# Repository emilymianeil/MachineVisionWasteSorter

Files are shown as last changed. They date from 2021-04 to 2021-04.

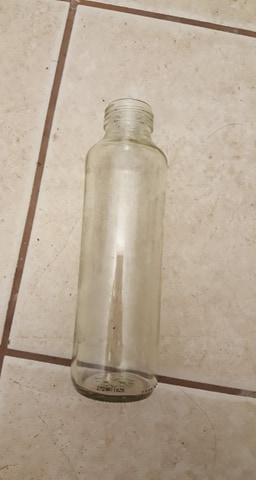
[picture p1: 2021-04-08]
Phase 3-Detail Design/4. Controls/Images/EG/Glass-Clear Bottles/155523304_348365116399683_3477293320346777046_n.jpg

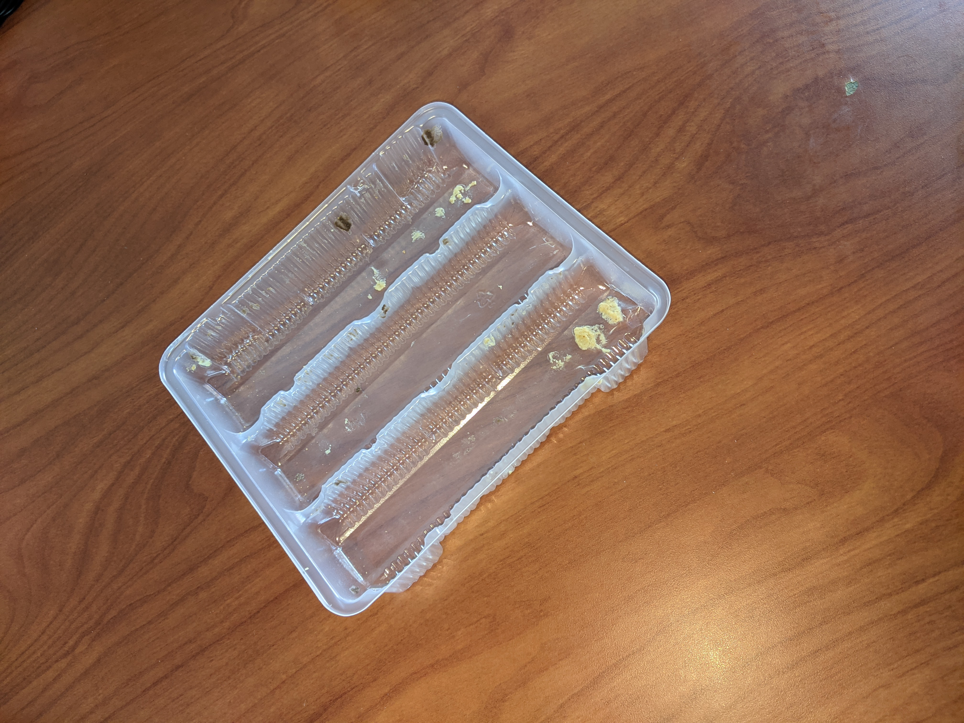
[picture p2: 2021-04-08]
Phase 3-Detail Design/4. Controls/Images/EG/Plastic-Clear/PXL_20210303_194455637.jpg

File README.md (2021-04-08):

# WasteSorter
The group chose to address the Canadian Engineering Grand Challenge’s (EGC) call for inclusive, safe, and sustainable cities by reducing recycling contamination and at improving the accuracy of at home recycling.

The primary function of the project is to take a piece of household waste, identify the type of waste, and sort it into its respective category. The design goals considered safety, environmental impact, public acceptance, reliability, performance, ease of use, maintenance, and standardization. The design criteria specifications were sorting accuracy, composition of product, safety standards, lifespan, cost, sorting, power consumption, system complexity.

To use the product, users must download the controls software onto a Jetson. Users then must 3D print or manufacture parts, order the custom PCB, and assemble the electro-mechanical system. Finally, the user must download the mobile application, and connect to the Jetson via Bluetooth.

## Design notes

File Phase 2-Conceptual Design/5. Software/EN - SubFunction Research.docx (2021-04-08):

# Executive Summary – Solution Evaluation

The following sub-functions were rated against each criteria by the ‘average’ solutions; I just put an estimate of how the common solution will perform, and then we can actually decide what specific solution we want and/or conduct further research to find the best tool for our team.

Specification | Image Processing | | IoT + App/Website | | Voice Commands | | Gesture Control | | Microprocessor
Sorting accuracy | >=75% | 10 | N/A | 10 | N/A | 10 | N/A | 10 | N/A | 10
Composition | N/A | 10 | N/A | 10 | N/A | 10 | Raw material | 0 | Raw material | 0
Safety Standards | ? | ? | ? | ? | ? | ? | Met (Jetson Nano) | 10 | Met | 10
Lifespan | N/A | 10 | N/A | 10 | N/A (depending on input) | 10 | ?? | 10 | ~5 yrs | 5
Cost | $0 | 10 | $35-$110 | 5 | $0-$7 | 9 | $100 | 2 | $25-$100 | 5
Sorting | ~2-5 seconds | 5 | ~2-5 seconds (TCP) | 5 | N/A | 10 | N/A | 10 | ~2-5 seconds (TCP + BT/Wifi) | 5
Power consumption | 7-12V | 7 | N/A (cloud computing) | 10 | N/A | 10 | 5V | 10 | 7-12V | 7
System Complexity | Requires Cam | 8 | Requires BT/wifi + cloud | 7 | Easy implementation | 9 | Good | 9 | Required for most functions | 8

*Note: photos for image detection (Trashnet) were taken by an iPhone 5, iPHone 7 and iPhone SE. If we choose this solution, we need to either use common phone, or use a camera with similar specifications if we are assuming the same efficacy rate. If not, we need to train the model with an entirely new set to get an efficacy rate.

*Note: Microprocessor can be used for LCD+Buttons, Touch Screen, loT+App/Website, general logic

*Note: I’m assuming a cost of $0 for phone usage (assuming user already has phone)

**Need to find lifespan of Jetson nano

# Sub-Function Solutions Research

## A. Identification – Image Processing

Image processing for waste exists online for free. The following are public Github repos with brief descriptions.

### I. Waste Sorter

Capabilities: Sorts images of into cardboard, glass, metal, paper, plastic, trash at a success rate of 92%. Uses fatsia deep learning framework.

Requirements: Given source files, corresponding dataset (available on the Github README), and Anaconda IDE (free python IDE)

Repository: https://github.com/collindching/Waste-Sorter

### II. Trash Recycling Classifier

Capabilities: Sorts images of into cardboard, glass, metal, paper, plastic, trash. Uses pytorch deep learning framework. Efficiency unknown.

Requirements: Given source files, corresponding dataset (available on the Github README, cloud environment for training (AWS or Google colab).

Repository: https://github.com/winkhai/trash-recycling-classifier

### III. Recycle

Capabilities: Sorts images of glass, metal, and plastic at a success rate of 85%. Uses

Requirements: Given source files, corresponding dataset (available on the Github README), and a python IDE

Repository: https://github.com/ZAFERSHAMIM/recycle

### IV. Trashnet

Capabilities: Sorts images of glass, paper, cardboard, plastic metal and trash at a success rate of 75%. Devices used to take dataset photos were common phones (iPhone 7, iPhone 5, iPHone SE).

Requirements: Given source files, corresponding dataset (available on the Github README), and a python IDE

Repository: https://github.com/garythung/trashnet

## B. IoT + App / Website

We can make an app for free using third party tools or manually (XCode, VS Code)

### I. Android App Builder – MIT App Inventor / App Builder / CodeUp Start

Capabilities: Minimal, low code environments with networking, scalable, compatible with most cloud environments

Cost: $25 (to publish to Google Play)

Source:

https://www.producthunt.com/alternatives/google-app-maker

https://appinventiv.com/blog/how-to-submit-app-to-google-play-store/#:~:text=There%20is%20only%20a%20one,you%20publish%20are%20cost%2Dfree

### II. Apple App Builder – MIT App Inventor / App Builder / CodeUp Start

Capabilities: Minimal, low code environments with networking, scalable, compatible with most cloud environments

Cost: $99 (to publish to App Store)

Source: https://codewithchris.com/submit-your-app-to-the-app-store/#:~:text=In%20order%20to%20be%20able,in%20the%20Apple%20Developer%20Program.&text=It%20costs%20%2499%2Fyear%20but,Stores%20on%20all%20Apple%20platforms

### III. Manual App Builder – XCode / VS Code

Capabilities: High code environments with networking, scalable, compatible with most cloud environments (but a lot of boiler plate code)

Cost: $0

Source: Me

### IV. Cloud Environments – Google / AWS

Capabilities: App engine + Cloud DB servers + Cloud SQL

Cost: $11 / month (24/7 access)

Source: https://cloud.google.com/products/calculator#id=89a14829-8f1e-4f0e-846f-7fc8f00ab297

## C. Voice Commands

These can be implemented using free APIs either on from an app or on the microprocessor directly. We need to make that decision, and cost will be decided accordingly. Note some microprocessors already have audio input.

### I. Web API – React API (for apps or microprocessor)

Capabilities: Flexible / programmable voice commands, relatively easy to install with npm

Cost: $0 (apart from either phone or microphone on microprocessor)

Source: https://medium.com/better-programming/how-to-implement-voice-command-in-your-react-app-f226edb2f202

### II. Microprocessor – Microphrone

Capabilities: continuous input, 40dB or 50dB , 1.25V bias

Cost: ~$7

Source: https://www.adafruit.com/product/1713

## D. Gesture Control

We would need a processor that already has gesture control capabilities (it’s too much boiler plate / overhead to implement within 2 months). Most notable microprocessor capable of this is the NVIDIA Jetson Nano. See the appropriate section for all the info.

# Extraneous

## A. Logic – Microprocessors

### I. Raspberry Pi

Specifications: made from raw materials, average 5 year lifespan

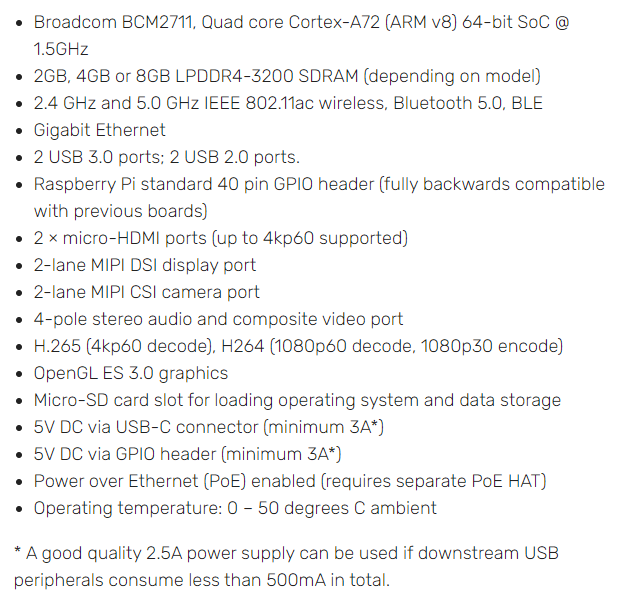
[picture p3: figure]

Cost: ~$35

Source: https://raspberrypi.stackexchange.com/questions/38321/raspberry-pi-lifespan-reliability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,autoreboot%2C%20and%20good%20SD%20cards.

http://www.designlife-cycle.com/raspberry-pi https://www.raspberrypi.org/products/raspberry-pi-4-model-b/specifications/

### II. Arduino

Specifications:

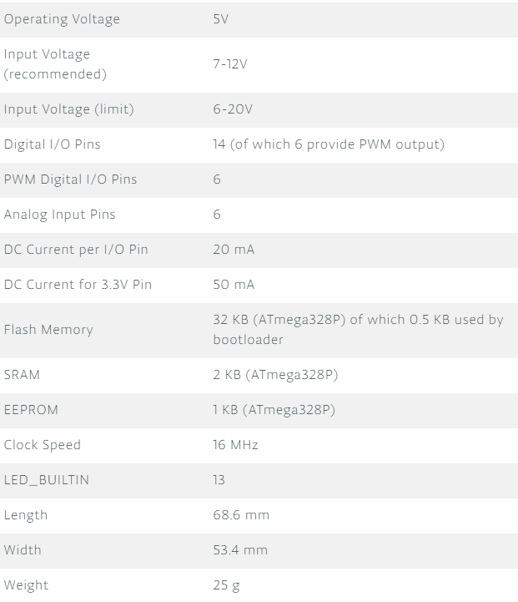
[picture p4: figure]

Cost: ~$20

Source: https://store.arduino.cc/usa/arduino-uno-rev3

### III. Jetson Nano

Specifications: 5V consumption

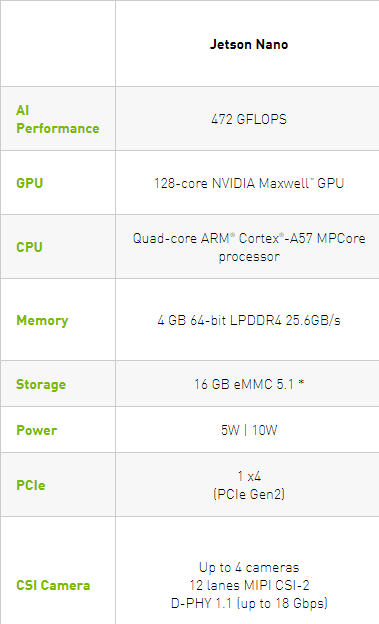
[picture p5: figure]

Cost: ~$100

Source: https://www.nvidia.com/en-us/autonomous-machines/embedded-systems/jetson-nano/

https://www.ximea.com/support/wiki/apis/Jetson_Nano_Benchmarks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,offer%20(5V%20and%202A).

## B. UDP vs TCP Connections

I’m assuming TCP here because we don’t need the images to be sent super quickly and I’d imagine we don’t want to deal with lost packages/images and we also don’t want to compress images before sending.

**do we want to encrypt data ?? probably out of scope

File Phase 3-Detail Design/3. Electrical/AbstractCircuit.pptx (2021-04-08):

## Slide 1

Wall AC supply

Wall AC to 12V DC Transformer

Power Source
Power Management
Internal Device
Output

Power Flow

Control Flow

12V DC

9.5 A (max) fuse

12V DC to 5V DC Converter

Stepper Motor Driver

LED strip

Digital GPIO

PWM dimmer

Stepper Motor

5V DC

Limit Switch

Jetson Nano 2GB

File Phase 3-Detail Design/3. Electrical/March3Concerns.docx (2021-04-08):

Concerns relating to electrical:

- Is all I’m doing power management and GPIO connections to motor drivers?
  - If so, I can provide a lot of support for someone else
  - I’ll contact Colin if he has any preferred GPIO pins for motor drivers, not a big deal (just retracing wires in schematic) so he can worry about more important controls things for now
- RESOLVED: I just realised that I’ve heard nothing about the sensor – informed Colin. Do I need to create any connections? (Still shouldn’t be that much work) NOPE, USB CABLE OR SIMILAR IS NOT PART OF THE ELECTRICAL DESIGN
- Just a few things that require more research on my part, not a macro concern for group, putting them here to list them somewhere:
  - Which way around do motors connect to drivers?
  - Step down converter provide sufficient current without overheating?
- Should I be purchasing parts to verify that they work? How soon?
- PCB, Breadboard, Perf board? -> this can affect the parts selected

Other concerns:

- Physical location of everything can influence design – I know this is all iterative
- We should have this done by end of month (ish, preferably even sooner) so that we can spend time on the final report and design verification presentation video (yes, I know it’s in Gantt chart, but it might be worth emphasising how little time we have left)
- Other courses picking up the project pace, too – the sooner we can settle on a design, the better

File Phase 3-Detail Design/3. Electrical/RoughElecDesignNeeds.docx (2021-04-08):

Important decision: board developed will be a PCB (industry safe, foolproofing, modifiable circuits aren’t understandable to most end users, etc)

# Brain Interfacing – Jetson Nano 2GB Developer Kit

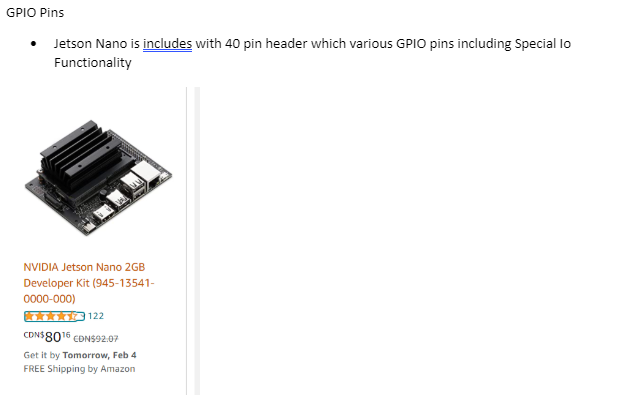
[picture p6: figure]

[1]

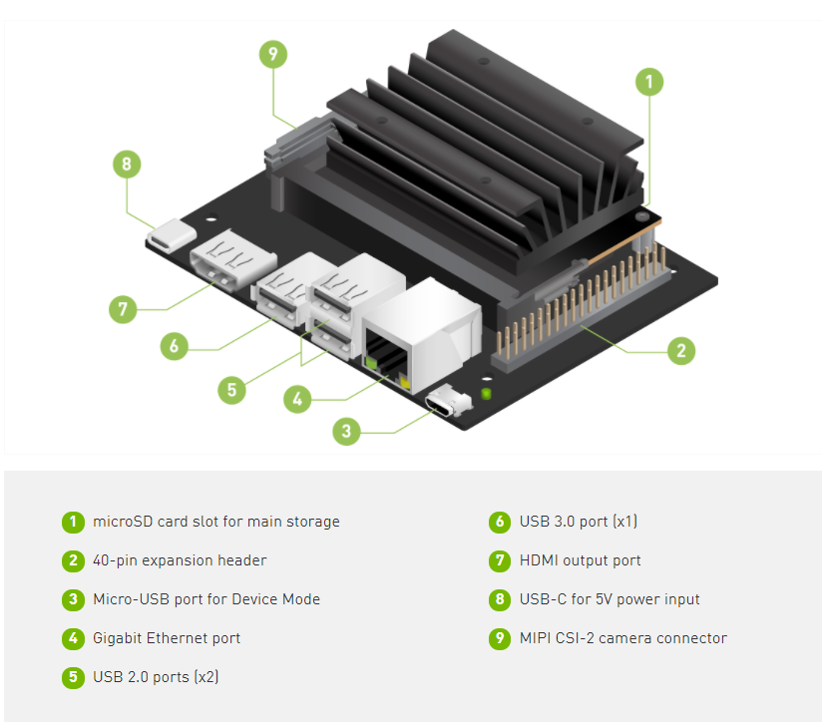
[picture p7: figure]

[2]

## Power

5W – 5V [2] Therefore max 1A? NOPE! SEE NEXT COUPLE OF LINES

USB-C takes 5V

Website says USB-C 5V 3A

Can be powered via two 5V pins at 2.5A each – pins 2&4 [3] NOT AT SAME TIME AS USB-C

## Control

40xpins, some of which are GPIO, I2C, I2S, SPI, PWM, UART

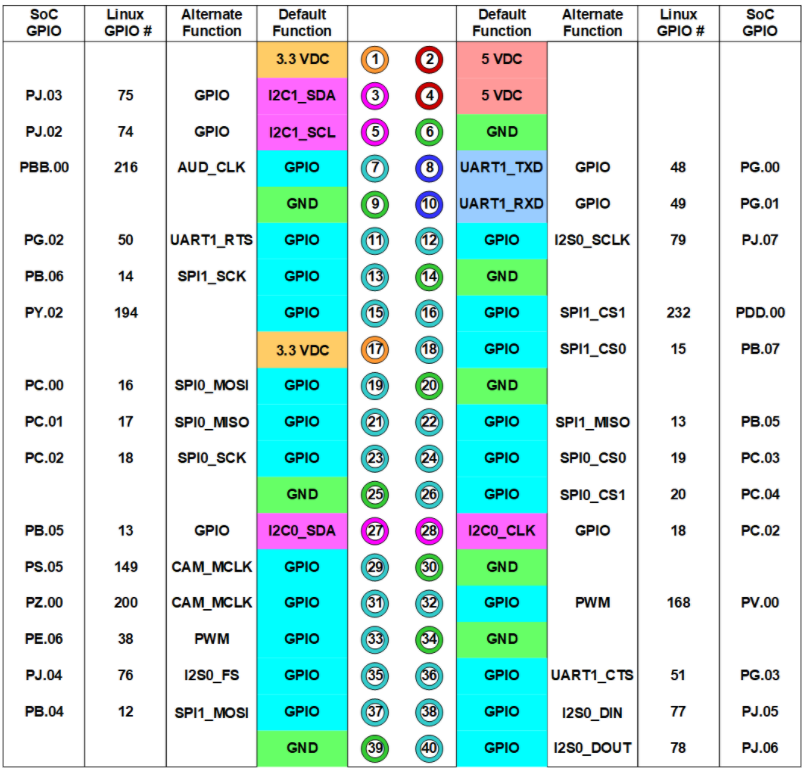
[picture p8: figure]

[3]

2xUSB 2.0

1xUSB 3.0

For now, ask controls if there is a preferred pin to control motors once I’ve figured out how many pins req’d to control motors

## Connections

2x40 female headers on electrical board input

2x40 male headers on electrical board output

## References

[1] Controls – Parts and Software Research

[2] https://developer.nvidia.com/embedded/learn/get-started-jetson-nano-2gb-devkit

[3] https://developer.nvidia.com/embedded/learn/jetson-nano-2gb-devkit-user-guide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

# Hardware Interfacing – Actuation

General design:

- Put things in
- Funnel centres things
- Need actuator to release funnel – ACTUATOR
- Chutes & diverter – ACTUATOR

Emily’s goal: 2 motors total

- PM suggested designing for expansion I.e. make 3 motors possible (DC DC converter needs to handle Jetson 2x 2.5A, motors 3x 0.35A

Stepper motor is strong at holding – likely enough for both

Current motor proposed: https://www.digikey.ca/en/products/detail/adafruit-industries-llc/324/5022791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

Much info about steppers available at https://cdn-learn.adafruit.com/downloads/pdf/all-about-stepper-motors.pdf

This is a Hybrid stepper – look for available drivers

All coils in phase energised together

## Power

V=12V, I=0.35A, R=34Ohm, L=33mH parameters given in datasheets

Low efficiency

## Control

How is stepper motor controlled? Several wires given. Pulse to rotate? How to counter-rotate?

Position feedback – limit switches/home detectors req’d for safety or to establish reference

- Promising limit switch: https://www.digikey.ca/en/products/detail/panasonic-electronic-components/ESE-11MH5T/354737
  - Sent to mech to verify that it is suitable

Adafruit Motor Shield drives up to 2 stepper motors, mounts onto Arduino but we ain’t using Arduino: https://cdn-learn.adafruit.com/downloads/pdf/adafruit-motor-shield-v2-for-arduino.pdf

2x this (https://www.digikey.ca/en/products/detail/adafruit-industries-llc/2448/5353672?productid=5353672) will do the trick for controlling one servo, $6.85 each

## Connections

non-mating crimp – secure connection; cheap; modifiable for testing purposes: link

Dismissed options: ring termnal (expensive, requires extra PCB modification to allow screw connection); (screw terminals – less secure as tension can pull wire out of grip)

# Power – Sum of Other Needs

Do we want to implement a button to turn the system on?

- Jetson 12-Pin Button Header can disable auto-system-on
- Power drain? Do we want to just put a switch in the power assembly?

Need 12V & 5V for motors/drivers and 5V for Jetson Nano

Jetson Nano needs up to 2.5A per pin

Motors need up to 0.35A each - how does Nano interface with motors? Adafruit driver found

Buck converter: https://www.digikey.ca/en/products/detail/intel/EC2650QI/10187118

- This converter has poor documentation

Buck converter: https://www.digikey.ca/en/products/detail/flex-power-modules/PMU8418-D/11581928

- Better documentation

Buck converter: https://www.digikey.ca/en/products/detail/bel-fuse-inc/VRAE-10E1A0G/1754625

- Testable (through hole, easily accessible terminals)
- Overkill for the application – future expansion e.g. adding motors

## Connections

Wall AC to 12Vdc wall wart, barrel jack in to board. Works for Arduino, works for this. Check current capacity before final choice.

# Future

Be sure of power

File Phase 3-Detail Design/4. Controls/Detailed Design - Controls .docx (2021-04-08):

Detailed Design: (Tasks)

- Add justification for scope limit:
- Go though the basic how it works and why.
  - Create a basic flowchart on how it works and this can be used in the final report.

NOTES:

- A basic overview of the control system is provided below.
- The detailed design and control algorithm is going to be shown in a flowchart. Emily Neil is going to help me work though that tomorrow (Wednesday Night) to see what software needs.

# Detailed Design – Controls AI – Image Recognition

# Section1: Objective

- Objective of the project is to increase the number of recyclables engineering the recycling stream
- To do this we need to identify the type of item and process it accordingly
- The current and best method found to identify the recycling was using computer vision since most of the recycling that we will be sorting is common household items, this includes but is not limited too cans, plastic containers, paper, cardboard boxes, amazon packages and many more.
- Since most of the items that will be recycles are common items, AI though the form of image recognition was though to be the best method since the library could be created with common household items.

# Section 2: General Overview

The Image Recognition will be performed on the Jetson Nano 2GB with a USB V4L2 camera. The Jetson Nano will use Image Classification techniques to determine the recycling object and determine the material composition. To use the image classification a model will need to be created to compare the photo to it.

The basic process of the jetson is to determine the type of recycling and then trigger the sorter mechanism to move and sort the object into the correct bin. The Jetson has GPIO pins which are going to be used to control the output and sorting mechanism. GPIO pins are general purpose input output pins. These pins are assignable to be able to read or write digital or analog signal to other instruments or sensors.

The image classification model will be trained using transfer learning, this is a technique for re-training a DNN model on a new dataset. Instead of using a dedicated server or cloud instance to train an entire new model, the Jetson can be used to train a custom model of household recyclables by using a pre-trained network. The figure below shows how the model will be trained by looking at smaller sections of the image and then keep moving into larger sections to ensure that it understands and can recognize the image properly.

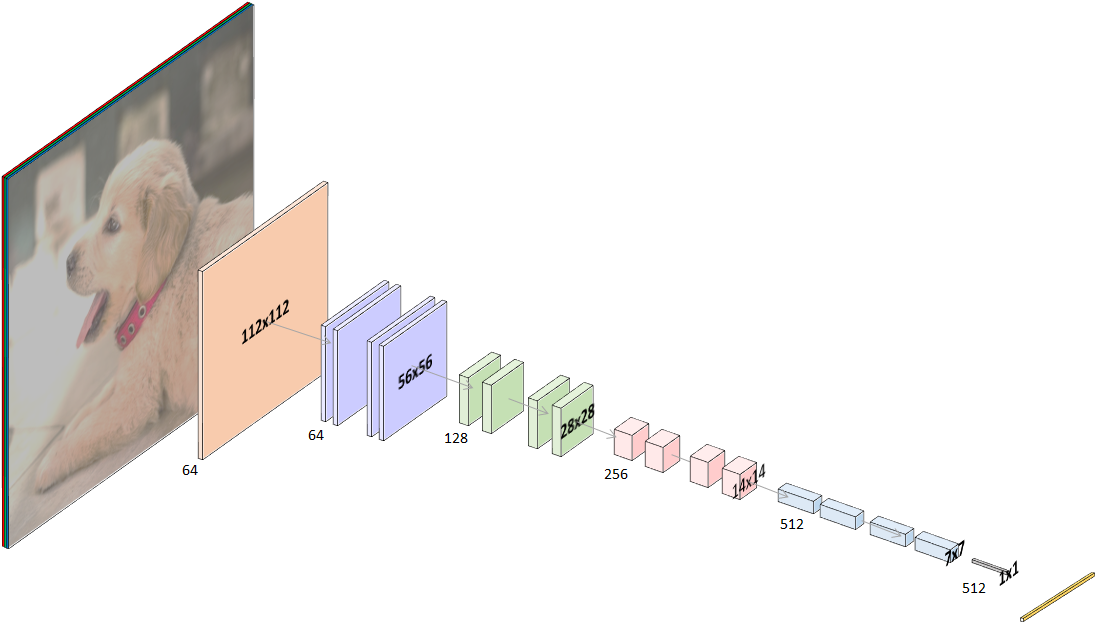
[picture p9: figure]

A simple python script will be used to run the images coming from the USB camera though the trained model to determine what the object is that is placed into the camera view. The python script will overlay the image class as well as the confidence level. The confidence level is how accurate the Jetson thinks the object is one of the classes. As stated in our objectives and constraints of the project, if the Jetson is not confident to a level of 80% the item will be sorted into the garbage. The model may not be accurate if the object is too different from the training database images or the lighting or other factor could cause the lack of certainty. The object will be placed into the garbage if the certainty level is not high enough to ensure that no waste is sorted into the wrong bin. It is better to not recycle something if you are unsure than to contaminate the entire pile of sorted recycling.

# Section 3: Detailed Overview

The following detailed overview section will go over a few different reasons and the process to using the Jetson Nano for the image classification process.

Sections:

1. Image Collection and Sorting

To create and build an image classification model, you will need images to train and test your model with to ensure its accuracy. For the project PyTorch was used to train the model used for the recycling sorter. The model needs hundreds and thousands of images to be able to have a good understanding of what the different classes are as well as how to distinguish between them.

PyTorch the training technique that we are using for creating the model requires the images to be split into 3 sections for each class of images. The 3 sections for each class that the images need to be split up into are, train, test, and validation. Each of the sections has an important purpose for training and creating the model. The train image-set should be able 80% of the total images that you have, this dataset is used for training the model and finding features and similarities between the different images to be able to create the model.

The validation image set is used to test but mainly validate the model that is created. PyTorch creates many models during the training processes and the computer needs a way to test itself to determine which model is the best. The training process uses the validation image set to test the model it has just created and comes up with a certainty rating. Based on the certainty rating the model can be kept or re-trained to be able to increase the certainty rating to a satisfaction level.

The test image data set is used for the programmer to test the model yourself. The computer will be able to test the model based on the validation data and determine if the model is accurately detecting the correct images. It is also useful to test different images to see how the model will respond.

2. Image Classification Model Training

To train the image classification model, transfer learning with PyTorch was used. Transfer learning was used since it takes less time and resources to train a model based on a new dataset compared to creating a model from scratch. When training with transfer learning, the weights of a pre-trained model are tuned to classify the new dataset. So, in our case, the ResNet-18 pre-trained model was used to help train the new model of recycling images.

During the training process, there are a few settings that could be changed to help train the model to improve accuracy. Some of the settings were changed to test if it would improve accuracy but then were returned to default values because they were providing the best results.

An important setting that needed to be changed was epoch. An epoch is one complete pass though the dataset of images though all classes. The default number of epoch’s is 35 which provides a great starting point for models because that is usually wear the model accuracy starts to level off as shown in the figure below for a Cat/Dog trained model. The figure shows that at around 30 epochs the dataset reaches about 80% accuracy and at 65 epoch’s the dataset converges at about 82.5% accuracy. The additional training time is helpful to improve model accuracy but the best way to improve model accuracy is to add more images to the training dataset.

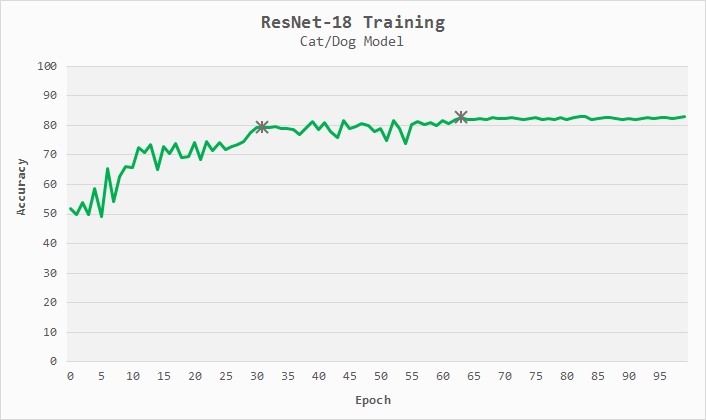
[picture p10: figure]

- It is important to know that the accuracy of the training model is determined by the validation image set, the model tests the image set with these validation images, so if you have images that are not performing well then you can put them into the validation image set to help pick the better model.
3. Image Classification Running

To be able to run the created image classification model, we need to convert it from the re-trained (transfer trained) ResNet-18 model to ONNX which is an open model format that supports most of the popular machine learning frameworks. A simple python script was used to convert the ResNet-18 model to a ONNX model that can be read by TensorRT which is what we use to process the images on the jetson in a python script.

The image classification technique that we are using supports both live camera feed though V4L2 USB cameras as well as .jpg image processing. The .jpg image processing was useful for testing of the model to ensure accuracy as well as to send a folder of images in at once to determine how it would react to them as well as keep a record of the images and the percentages for future training purposes.

4. Python Script – GPIO Pins – Output

A python script is used to run the image processing network which also puts the class it thinks it is as well as the accuracy level. The script will also determine when the item in the hopper has changed from just the background to an item class so that it will be able to trigger the motors and actuators to move the item into the correct bin. The sorting process will only begin after 10 confident guesses of 80% or more accuracy to ensure an item is ready to be sorted as well as ensure that the image is classified correctly. If the software detects that an object is there but the confidence interval on the type of recycling is not high enough to meet the threshold of 80% for 20 guesses (frames) then the item will be sorted to garbage to ensure that that no containments will be put into the recycling and cause problems later though the recycling process.

Within the python script the GPIO (input and output signals) pins are able to be signaled to provide the input and output signals to the motors and actuators to which are used to control the movement of the sorting mechanism. The script will determine when an item is ready to be sorted and placed into a bin after following the criteria shown above.

The python script will also send the information to the app over a Bluetooth connection. The app is what is used for the user to interact with the Jetson Nano (controller). The python script though the help of a Bluetooth USB dongle will open a connection with the phone and then be able to send the information to the phone app. The information that will be sent to the phone is the recycling class for the current image as well as the accuracy percentage, the user will also be able to see on the app the status of the current and past 100 items recycled and sorted to be able to check their log and how accurate the detection method is.

# Section 4: Process Detailed

Emily Neil and I are going to work on some more flowcharts and process steps tomorrow (Wednesday Night) to ensure that Bill will understand and know what the controls is planning to do as well as how to interact with the software (app).

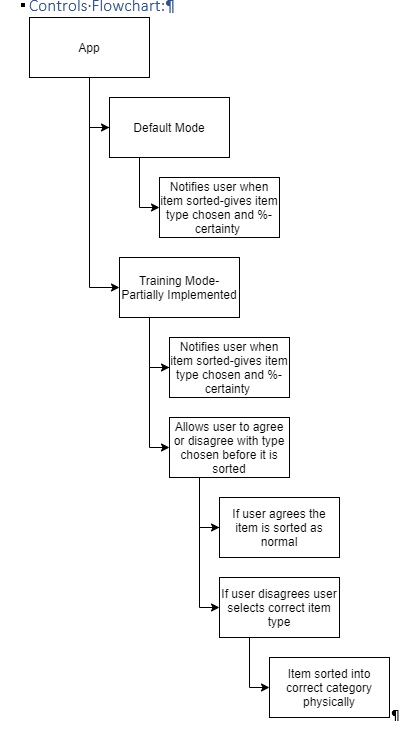
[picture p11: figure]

# References:

https://towardsdatascience.com/how-to-train-an-image-classifier-in-pytorch-and-use-it-to-perform-basic-inference-on-single-images-99465a1e9bf5

https://github.com/dusty-nv/jetson-inference/blob/master/docs/pytorch-transfer-learning.md

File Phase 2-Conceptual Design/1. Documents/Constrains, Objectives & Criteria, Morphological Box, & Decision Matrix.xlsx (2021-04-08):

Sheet: Constraints & Objectives
No. | Type | Specification | Unit
1 | Constraint (inequality) | Must be >= 80% accurate at identifying/sorting paper, plastic, metal, glass, and “other” | % Number of Items
2 | Constraint | Must be made from >= 30% recycled material | % Composition
 | (inequality)
3 | Constraint | Must identify/sort >= 6 items in a minute | Items/Min
 | (inequality) | (one every 10 seconds)
4 | Constraint | Must cost <= $250 | CAD
 | (inequality)
5 | Constraint | Must accept items of up to size 15x15x30 cm rectangle | Volume
 | (inequality)
6 | Constraint (inequality) | Must weigh <= 25 Kg | Kg
7 | Constraint | Must not misidentify glass/Styrofoam/trash into other types more than 10% of the time* | % Items
 | (inequality)
8 | Constraint | Must meet all applicable Canadian safety standards | NA
 | (Yes/No)
9 | Constraint | Must be compatible with standard recycling/garbage bin sizes | NA
 | (Yes/No)
10 | Objective | Should be low power <= 50W | Watts
 | (inequality)
11 | Objective | Should have long lifespan >= 15Yr | Years
 | (inequality)
12 | Objective | Should fit in average Canadian appliance footprint for residential design | m2
 | (inequality)
13 | Objective (Yes/No) | Should be open source | NA
14 | Objective (Yes/No) | Should be modular | NA
15 | Objective (Yes/No) | Should be scalable | NA
16 | Objective (Yes/No) | All parts should be available locally/within Canada | NA

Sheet: Brainstorming
Rejected | Reason | Sub-Functions | Component Alternatives
Chemical | Not safe or sustainable | Identification | Light Sensor | Conductivity | Image Recognition | Ultrasonic & accelerometer | Hall Effect | Capacitive | Inductive | Chemical | Hardness | Physical Strength | Flammability
Hardness | Desctructive testing is not safe, nor would it be effective for many recyclable materials | Power | Wall power + DC converter | Battery | Solar | User Powered | Nuclear | Fuell Cell
Physical Strength | Desctructive testing is not safe, nor would it be effective for many recyclable materials | User Interface | Lights + buttons | Touchscreen | LCD + Buttons | IOT + App/Website | Mechanical | Voice Commands/Speaker | Gesture Control
Flammability | Not safe, also would cause damage to recyclables | Sorting
Solar | Device is for inside operation | Actuator | Pneumatics | Hydraulics | Piston | Ramp+gravity | Funnel | Conveyor | Moving Platform | Sweeper | Pick & Place arm | Shaker | Rollers
User Powered | Would not be automatic | Input | Hatch & Lock | Chute | Open Face | Drawer | Electric drive input | Hopper + gate | Flap | Basketball net (gamify recycling) | Vacuum | Mining Buckets
Nuclear | Would not be safe | Output | Flap | Chutes | Electric drives | Open Face | Pneumatics | Manual | Moving Arm
Fuell Cell | Explosives are not safe
Pneumatics(inp) | Compressed air not safe
Hydraulics | Would not meet Canadian safety standards (Energy)
Pick & Place Arm | Expensive
Shaker | Would not meet Canadian safety standards (sound)
Open Face(inp) | Access to machine while working not safe
Vacuum | Would not be able to handle large items
Open Face(out) | Access to machine while working not safe
Pneumatics(out) | Compressed air not safe
Manual | Not automatic
Rejected | Reason | Sub-Functions | Component Alternatives
Hall Effect | Can't differentiate multiple types | Identification | Light Sensor | Conductivity | Image Recognition | Ultrasonic & accelerometer | Hall Effect | Capacitive | Inductive
Capaciitive | Can't differentiate multiple types | Power | Wall power + DC converter | Battery
Inductive | Can't differentiate multiple types | User Interface | Lights + buttons | Touchscreen | LCD + Buttons | IOT + App/Website | Voice Commands/Speaker | Gesture Control
Battery | Not recyclable at EOL | Sorting
Lights + buttons | Complicated for user | Actuator | Piston | Ramp+gravity | Funnel | Conveyor | Moving Platform | Sweeper | Rollers
Voice Commands/Speaker | Required hardware is expensive | Input | Hatch & Lock | Chute | Drawer | Electric drive input | Hopper + gate | Flap | Basketball net (gamify recycling) | Mining Buckets
Gesture Control | Required hardware is expensive | Output | Flap + Diverter | Chutes + Diverter | Electric drives | Moving Platform
Conveyor | Many moving parts
Moving Platform(actuator) | Many moving parts
Electric drive input | Expensive
Basketball Net | Throwing glass not safe
Mining buckets | Many moving parts
Electric drive output | Expensive
Moving Platform output | Many moving parts
Rejected | Reason | Sub-Functions | Component Alternatives
Light Sensor | Need to combine all to manage the material types present | Identification | Light Sensor | Conductivity | Image Recognition | Ultrasonic & accelerometer
Conductivity |  | Power | Wall power + DC converter
Ultrasonic+Accelerometer |  | User Interface | Touchscreen | LCD + Buttons | IOT + App/Website
Touchscreen | Removed as added complexity for software is not warrented | Sorting
LCD + Buttons | Removed to reduce number of parts needed | Actuator | Piston | Ramp+gravity | Funnel | Sweeper | Rollers
Rollers | Too many moving parts in the bearings | Input | Hatch & Lock | Chute | Drawer | Hopper + gate | Flap
Hopper+Gate | To large for residential settings, no need to overcomplicate | Output | Flap + Diverter | Chutes + Diverter

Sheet: Morphological Chart
Chart 1 |  |  |  |  |  |  | Chart 2 |  |  |  |  |  |  | Chart 2
Alternative | Subfuntion |  |  |  |  |  | Alternative | Subfuntion |  |  |  |  |  | Alternative | Subfuntion
 | Identification | Power | UI | Actuator | Input | Output |  | Identification | Power | UI | Actuator | Input | Output |  | Identification | Power | UI | Actuator | Input | Output
1 | Light Sensor | Wall power + DC converter | Lights + buttons | Piston | Hatch & Lock | Flap + Diverter | 1 | Light Sensor | Wall power + DC converter | Touchscreen | Piston | Hatch & Lock | Flap + Diverter | 1 | Image Recognition | Wall power + DC converter | IOT + App/Website | Piston | Hatch & Lock | Chutes + Diverter
2 | Light Sensor | Wall power + DC converter | Lights + buttons | Piston | Hatch & Lock | Chutes + Diverter | 2 | Light Sensor | Wall power + DC converter | Touchscreen | Piston | Hatch & Lock | Chutes + Diverter | 2 | Image Recognition | Wall power + DC converter | IOT + App/Website | Piston | Hatch & Lock | Flap + Diverter
3 | Light Sensor | Wall power + DC converter | Lights + buttons | Piston | Hatch & Lock | Electric drives | 3 | Light Sensor | Wall power + DC converter | Touchscreen | Piston | Chute | Flap + Diverter | 3 | Image Recognition | Wall power + DC converter | IOT + App/Website | Piston | Chute | Chutes + Diverter
4 | Light Sensor | Wall power + DC converter | Lights + buttons | Piston | Hatch & Lock | Moving Arm | 4 | Light Sensor | Wall power + DC converter | Touchscreen | Piston | Chute | Chutes + Diverter | 4 | Image Recognition | Wall power + DC converter | IOT + App/Website | Piston | Chute | Flap + Diverter
5 | Light Sensor | Wall power + DC converter | Lights + buttons | Piston | Chute | Flap + Diverter | 5 | Light Sensor | Wall power + DC converter | Touchscreen | Piston | Drawer | Flap + Diverter | 5 | Image Recognition | Wall power + DC converter | IOT + App/Website | Piston | Drawer | Chutes + Diverter
6 | Light Sensor | Wall power + DC converter | Lights + buttons | Piston | Chute | Chutes + Diverter | 6 | Light Sensor | Wall power + DC converter | Touchscreen | Piston | Drawer | Chutes + Diverter | 6 | Image Recognition | Wall power + DC converter | IOT + App/Website | Piston | Drawer | Flap + Diverter
7 | Light Sensor | Wall power + DC converter | Lights + buttons | Piston | Chute | Electric drives | 7 | Light Sensor | Wall power + DC converter | Touchscreen | Piston | Hopper + gate | Flap + Diverter | 7 | Image Recognition | Wall power + DC converter | IOT + App/Website | Piston | Flap | Chutes + Diverter
8 | Light Sensor | Wall power + DC converter | Lights + buttons | Piston | Chute | Moving Arm | 8 | Light Sensor | Wall power + DC converter | Touchscreen | Piston | Hopper + gate | Chutes + Diverter | 8 | Image Recognition | Wall power + DC converter | IOT + App/Website | Piston | Flap | Flap + Diverter
9 | Light Sensor | Wall power + DC converter | Lights + buttons | Piston | Drawer | Flap + Diverter | 9 | Light Sensor | Wall power + DC converter | Touchscreen | Piston | Flap | Flap + Diverter | 9 | Image Recognition | Wall power + DC converter | IOT + App/Website | Ramp+gravity (Raise/Lower) | Hatch & Lock | Chutes + Diverter
10 | Light Sensor | Wall power + DC converter | Lights + buttons | Piston | Drawer | Chutes + Diverter | 10 | Light Sensor | Wall power + DC converter | Touchscreen | Piston | Flap | Chutes + Diverter | 10 | Image Recognition | Wall power + DC converter | IOT + App/Website | Ramp+gravity (Raise/Lower) | Hatch & Lock | Flap + Diverter
11 | Light Sensor | Wall power + DC converter | Lights + buttons | Piston | Drawer | Electric drives | 11 | Light Sensor | Wall power + DC converter | Touchscreen | Ramp+gravity | Hatch & Lock | Flap + Diverter | 11 | Image Recognition | Wall power + DC converter | IOT + App/Website | Ramp+gravity (Raise/Lower) | Chute | Chutes + Diverter
12 | Light Sensor | Wall power + DC converter | Lights + buttons | Piston | Drawer | Moving Arm | 12 | Light Sensor | Wall power + DC converter | Touchscreen | Ramp+gravity | Hatch & Lock | Chutes + Diverter | 12 | Image Recognition | Wall power + DC converter | IOT + App/Website | Ramp+gravity (Raise/Lower) | Chute | Flap + Diverter
13 | Light Sensor | Wall power + DC converter | Lights + buttons | Piston | Electric drive input | Flap + Diverter | 13 | Light Sensor | Wall power + DC converter | Touchscreen | Ramp+gravity | Chute | Flap + Diverter | 13 | Image Recognition | Wall power + DC converter | IOT + App/Website | Ramp+gravity (Raise/Lower) | Drawer | Chutes + Diverter
14 | Light Sensor | Wall power + DC converter | Lights + buttons | Piston | Electric drive input | Chutes + Diverter | 14 | Light Sensor | Wall power + DC converter | Touchscreen | Ramp+gravity | Chute | Chutes + Diverter | 14 | Image Recognition | Wall power + DC converter | IOT + App/Website | Ramp+gravity (Raise/Lower) | Drawer | Flap + Diverter
15 | Light Sensor | Wall power + DC converter | Lights + buttons | Piston | Electric drive input | Electric drives | 15 | Light Sensor | Wall power + DC converter | Touchscreen | Ramp+gravity | Drawer | Flap + Diverter | 15 | Image Recognition | Wall power + DC converter | IOT + App/Website | Ramp+gravity (Raise/Lower) | Flap | Chutes + Diverter
16 | Light Sensor | Wall power + DC converter | Lights + buttons | Piston | Electric drive input | Moving Arm | 16 | Light Sensor | Wall power + DC converter | Touchscreen | Ramp+gravity | Drawer | Chutes + Diverter | 16 | Image Recognition | Wall power + DC converter | IOT + App/Website | Ramp+gravity (Raise/Lower) | Flap | Flap + Diverter
17 | Light Sensor | Wall power + DC converter | Lights + buttons | Piston | Hopper + gate | Flap + Diverter | 17 | Light Sensor | Wall power + DC converter | Touchscreen | Ramp+gravity | Hopper + gate | Flap + Diverter | 17 | Image Recognition | Wall power + DC converter | IOT + App/Website | Funnel | Hatch & Lock | Chutes + Diverter
18 | Light Sensor | Wall power + DC converter | Lights + buttons | Piston | Hopper + gate | Chutes + Diverter | 18 | Light Sensor | Wall power + DC converter | Touchscreen | Ramp+gravity | Hopper + gate | Chutes + Diverter | 18 | Image Recognition | Wall power + DC converter | IOT + App/Website | Funnel | Hatch & Lock | Flap + Diverter
19 | Light Sensor | Wall power + DC converter | Lights + buttons | Piston | Hopper + gate | Electric drives | 19 | Light Sensor | Wall power + DC converter | Touchscreen | Ramp+gravity | Flap | Flap + Diverter | 19 | Image Recognition | Wall power + DC converter | IOT + App/Website | Funnel | Chute | Chutes + Diverter
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

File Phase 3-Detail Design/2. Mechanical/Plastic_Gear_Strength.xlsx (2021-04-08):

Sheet: 0.75_mod_25_teeth
Variable | Value | Units | Description |  | Note: Cells highlighted in yellow are independent parameters/variables
Ng | 100 |  | Number of teeth - gear
Np | 25 |  | Number of teeth - pinion
F | 4.723986453 | lbf | Tangential tooth loading at pitch line
Pd | 33.86664838 | /in | Diametral pitch
Y | 0.579 |  | Lewis form factor for plastic gears, loaded at the pitch point
Wt | 4.723986453 | lbf | Transmitted load
Dp | 0.738189375 | in | Pitch diameter, pinion
mu | 0.32 |  | Poisson's ratio
E | 333586.6658 | psi | Modulus of Elasticity
phi | 0.3490658504 | Radians | Pressure angle
m | 4 |  | Speed Ratio, Ng/Np
fw | 0.29527575 | in
Metric Variable
E_m | 2300000000 | Pa | Modulus of Elasticity, metric
Pd_m | 1.333333333 | /mm | Diametral pitch, metric
Dp_m | 18.75 | mm | Pitch diameter, pinion, metric
Wt_m | 21.01333333 | N | Transmitted load, metric
module | 0.75 | mm | Module
fw_m | 7.5 | mm | Face width (recommended 3-5x circular pitch)
circ_pitch | 2.35619449 | mm | Circular pitch
F_m | 21.01333333 | N | Tangential tooth loading at pitch line, metric
T | 0.197 | Nm | Transmitted torque
Bending Stress, Sb | 935.7816338 | psi
Contact Stress, SH | 3157.772041 | psi
Sb, metric | 6451989.778 | Pa | 6.451989778 | Mpa
SH, metric | 21772080.35 | Pa | 21.77208035 | Mpa
Intermediate calculations for contact stress:
a1 | 21.67270264
a2 | 59148.80438
a3 | 7.778619134

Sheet: 0.75_mod_25_teeth (2)
Variable | Value | Units | Description |  | Note: Cells highlighted in yellow are independent parameters/variables
Ng | 25 |  | Number of teeth - gear
Np | 25 |  | Number of teeth - pinion
F | 4.723986453 | lbf | Tangential tooth loading at pitch line
Pd | 33.86664838 | /in | Diametral pitch
Y | 0.579 |  | Lewis form factor for plastic gears, loaded at the pitch point
Wt | 4.723986453 | lbf | Transmitted load
Dp | 0.738189375 | in | Pitch diameter, pinion
mu | 0.32 |  | Poisson's ratio
E | 333586.6658 | psi | Modulus of Elasticity
phi | 0.3490658504 | Radians | Pressure angle
m | 1 |  | Speed Ratio, Ng/Np
fw | 0.29527575 | in
Metric Variable
E_m | 2300000000 | Pa | Modulus of Elasticity, metric
Pd_m | 1.333333333 | /mm | Diametral pitch, metric
Dp_m | 18.75 | mm | Pitch diameter, pinion, metric
Wt_m | 21.01333333 | N | Transmitted load, metric
module | 0.75 | mm | Module
fw_m | 7.5 | mm | Face width (recommended 3-5x circular pitch)
circ_pitch | 2.35619449 | mm | Circular pitch
F_m | 21.01333333 | N | Tangential tooth loading at pitch line, metric
T | 0.197 | Nm | Transmitted torque
Bending Stress, Sb | 935.7816338 | psi
Contact Stress, SH | 3994.300792 | psi
Sb, metric | 6451989.778 | Pa | 6.451989778 | Mpa
SH, metric | 27539745.33 | Pa | 27.53974533 | Mpa
Intermediate calculations for contact stress:
a1 | 21.67270264
a2 | 59148.80438
a3 | 12.44579061

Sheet: 1_mod_100_teeth
Variable | Value | Units | Description |  | Note: Cells highlighted in yellow are independent parameters/variables
Ng | 100 |  | Number of teeth - gear
Np | 25 |  | Number of teeth - pinion
F | 2.791543277 | lbf | Tangential tooth loading at pitch line
Pd | 25.39998628 | /in | Diametral pitch
Y | 0.758 |  | Lewis form factor for plastic gears, loaded at the pitch point
Wt | 2.791543277 | lbf | Transmitted load
Dp | 0.9842525 | in | Pitch diameter, pinion
Dg | 3.93701 | in | Pitch diameter, gear
mu | 0.32 |  | Poisson's ratio
E | 333586.6658 | psi | Modulus of Elasticity
phi | 0.3490658504 | Radians | Pressure angle
m | 4 |  | Speed Ratio, Ng/Np
fw | 0.393701 | in
Metric Variable
E_m | 2300000000 | Pa | Modulus of Elasticity, metric
Pd_m | 1 | /mm | Diametral pitch, metric
Dp_m | 25 | mm | Pitch diameter, pinion, metric
Dg_m | 100 | mm | Pitch diameter, gear, metric
Wt_m | 12.4174 | N | Transmitted load, metric
module | 1 | mm | Module
fw_m | 10 | mm | Face width (recommended 3-5x circular pitch)
circ_pitch | 3.141592654 | mm | Circular pitch
F_m | 12.4174 | N | Tangential tooth loading at pitch line, metric
T | 0.62087 | Nm | Transmitted torque
Bending Stress, Sb | 237.5976405 | psi
Contact Stress, SH | 910.2902762 | psi
Sb, metric | 1638178.708 | Pa | 1.638178708 | Mpa
SH, metric | 6276232.984 | Pa | 6.276232984 | Mpa
Intermediate calculations for contact stress:
a1 | 1.800990115
a2 | 59148.80438
a3 | 7.778619134

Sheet: 1_mod_25_teeth
Variable | Value | Units | Description |  | Note: Cells highlighted in yellow are independent parameters/variables
Ng | 100 |  | Number of teeth - gear
Np | 25 |  | Number of teeth - pinion
F | 2.791543277 | lbf | Tangential tooth loading at pitch line
Pd | 25.39998628 | /in | Diametral pitch
Y | 0.579 |  | Lewis form factor for plastic gears, loaded at the pitch point
Wt | 2.791543277 | lbf | Transmitted load
Dp | 0.9842525 | in | Pitch diameter, pinion
Dg | 3.93701 | in | Pitch diameter, gear
mu | 0.32 |  | Poisson's ratio
E | 333586.6658 | psi | Modulus of Elasticity
phi | 0.3490658504 | Radians | Pressure angle
m | 4 |  | Speed Ratio, Ng/Np
fw | 0.393701 | in
Metric Variable
E_m | 2300000000 | Pa | Modulus of Elasticity, metric
Pd_m | 1 | /mm | Diametral pitch, metric
Dp_m | 25 | mm | Pitch diameter, pinion, metric
Dg_m | 100 | mm | Pitch diameter, gear, metric
Wt_m | 12.4174 | N | Transmitted load, metric
module | 1 | mm | Module
fw_m | 10 | mm | Face width (recommended 3-5x circular pitch)
circ_pitch | 3.141592654 | mm | Circular pitch
F_m | 12.4174 | N | Tangential tooth loading at pitch line, metric
T | 0.1552175 | Nm | Transmitted torque
Bending Stress, Sb | 311.0518334 | psi
Contact Stress, SH | 1820.580552 | psi
Sb, metric | 2144627.739 | Pa | 2.144627739 | Mpa
SH, metric | 12552465.97 | Pa | 12.55246597 | Mpa
Intermediate calculations for contact stress:
a1 | 7.203960461
a2 | 59148.80438
a3 | 7.778619134

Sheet: 1_mod_25_teeth (2)
Variable | Value | Units | Description |  | Note: Cells highlighted in yellow are independent parameters/variables
Ng | 25 |  | Number of teeth - gear
Np | 25 |  | Number of teeth - pinion
F | 2.791543277 | lbf | Tangential tooth loading at pitch line
Pd | 25.39998628 | /in | Diametral pitch
Y | 0.579 |  | Lewis form factor for plastic gears, loaded at the pitch point
Wt | 2.791543277 | lbf | Transmitted load
Dp | 0.9842525 | in | Pitch diameter, pinion
Dg | 0.9842525 | in | Pitch diameter, gear
mu | 0.32 |  | Poisson's ratio
E | 333586.6658 | psi | Modulus of Elasticity
phi | 0.3490658504 | Radians | Pressure angle
m | 1 |  | Speed Ratio, Ng/Np
fw | 0.393701 | in
Metric Variable
E_m | 2300000000 | Pa | Modulus of Elasticity, metric
Pd_m | 1 | /mm | Diametral pitch, metric
Dp_m | 25 | mm | Pitch diameter, pinion, metric
Dg_m | 25 | mm | Pitch diameter, gear, metric
Wt_m | 12.4174 | N | Transmitted load, metric
module | 1 | mm | Module
fw_m | 10 | mm | Face width (recommended 3-5x circular pitch)
circ_pitch | 3.141592654 | mm | Circular pitch
F_m | 12.4174 | N | Tangential tooth loading at pitch line, metric
T | 0.1552175 | Nm | Transmitted torque
Bending Stress, Sb | 311.0518334 | psi
Contact Stress, SH | 2302.872484 | psi
Sb, metric | 2144627.739 | Pa | 2.144627739 | Mpa
SH, metric | 15877753.09 | Pa | 15.87775309 | Mpa
Intermediate calculations for contact stress:
a1 | 7.203960461
a2 | 59148.80438
a3 | 12.44579061

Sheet: 1_mod_50_teeth
Variable | Value | Units | Description |  | Note: Cells highlighted in yellow are independent parameters/variables
Ng | 50 |  | Number of teeth - gear
Np | 50 |  | Number of teeth - pinion
F | 5.583086553 | lbf | Tangential tooth loading at pitch line
Pd | 25.39998628 | /in | Diametral pitch
Y | 0.696 |  | Lewis form factor for plastic gears, loaded at the pitch point
Wt | 5.583086553 | lbf | Transmitted load
Dp | 1.968505 | in | Pitch diameter, pinion
Dg | 1.968505 | in | Pitch diameter, gear
mu | 0.32 |  | Poisson's ratio
E | 333586.6658 | psi | Modulus of Elasticity
phi | 0.3490658504 | Radians | Pressure angle
m | 1 |  | Speed Ratio, Ng/Np
fw | 0.393701 | in
Metric Variable
E_m | 2300000000 | Pa | Modulus of Elasticity, metric
Pd_m | 1 | /mm | Diametral pitch, metric
Dp_m | 50 | mm | Pitch diameter, pinion, metric
Dg_m | 50 | mm | Pitch diameter, gear, metric
Wt_m | 24.8348 | N | Transmitted load, metric
module | 1 | mm | Module
fw_m | 10 | mm | Face width (recommended 3-5x circular pitch)
circ_pitch | 3.141592654 | mm | Circular pitch
F_m | 24.8348 | N | Tangential tooth loading at pitch line, metric
T | 0.62087 | Nm | Transmitted torque
Bending Stress, Sb | 517.5258952 | psi
Contact Stress, SH | 2302.872484 | psi
Sb, metric | 3568216.841 | Pa | 3.568216841 | Mpa
SH, metric | 15877753.09 | Pa | 15.87775309 | Mpa
Intermediate calculations for contact stress:
a1 | 7.203960461
a2 | 59148.80438
a3 | 12.44579061

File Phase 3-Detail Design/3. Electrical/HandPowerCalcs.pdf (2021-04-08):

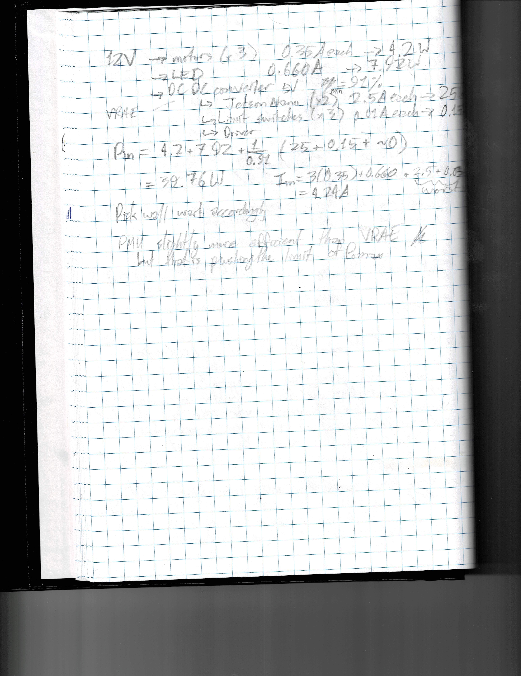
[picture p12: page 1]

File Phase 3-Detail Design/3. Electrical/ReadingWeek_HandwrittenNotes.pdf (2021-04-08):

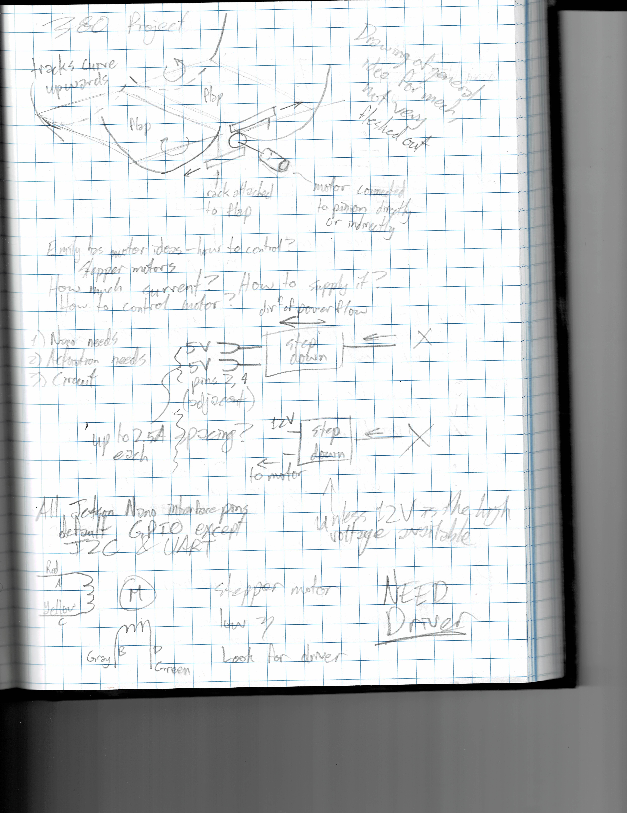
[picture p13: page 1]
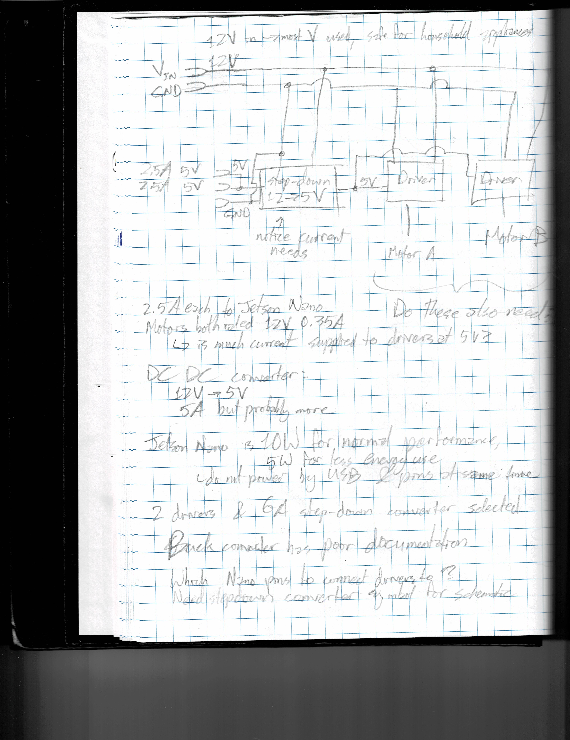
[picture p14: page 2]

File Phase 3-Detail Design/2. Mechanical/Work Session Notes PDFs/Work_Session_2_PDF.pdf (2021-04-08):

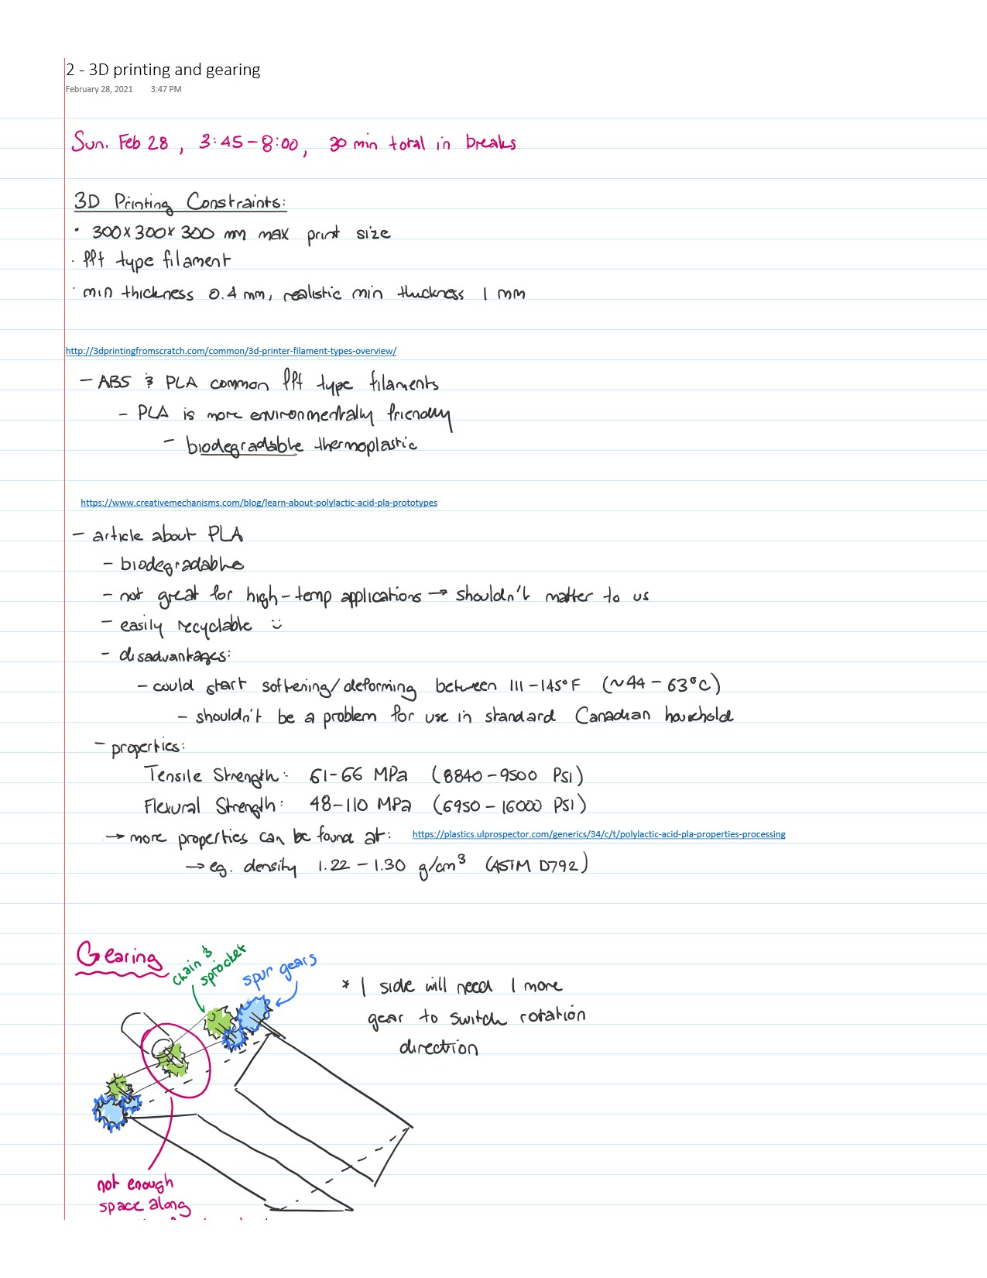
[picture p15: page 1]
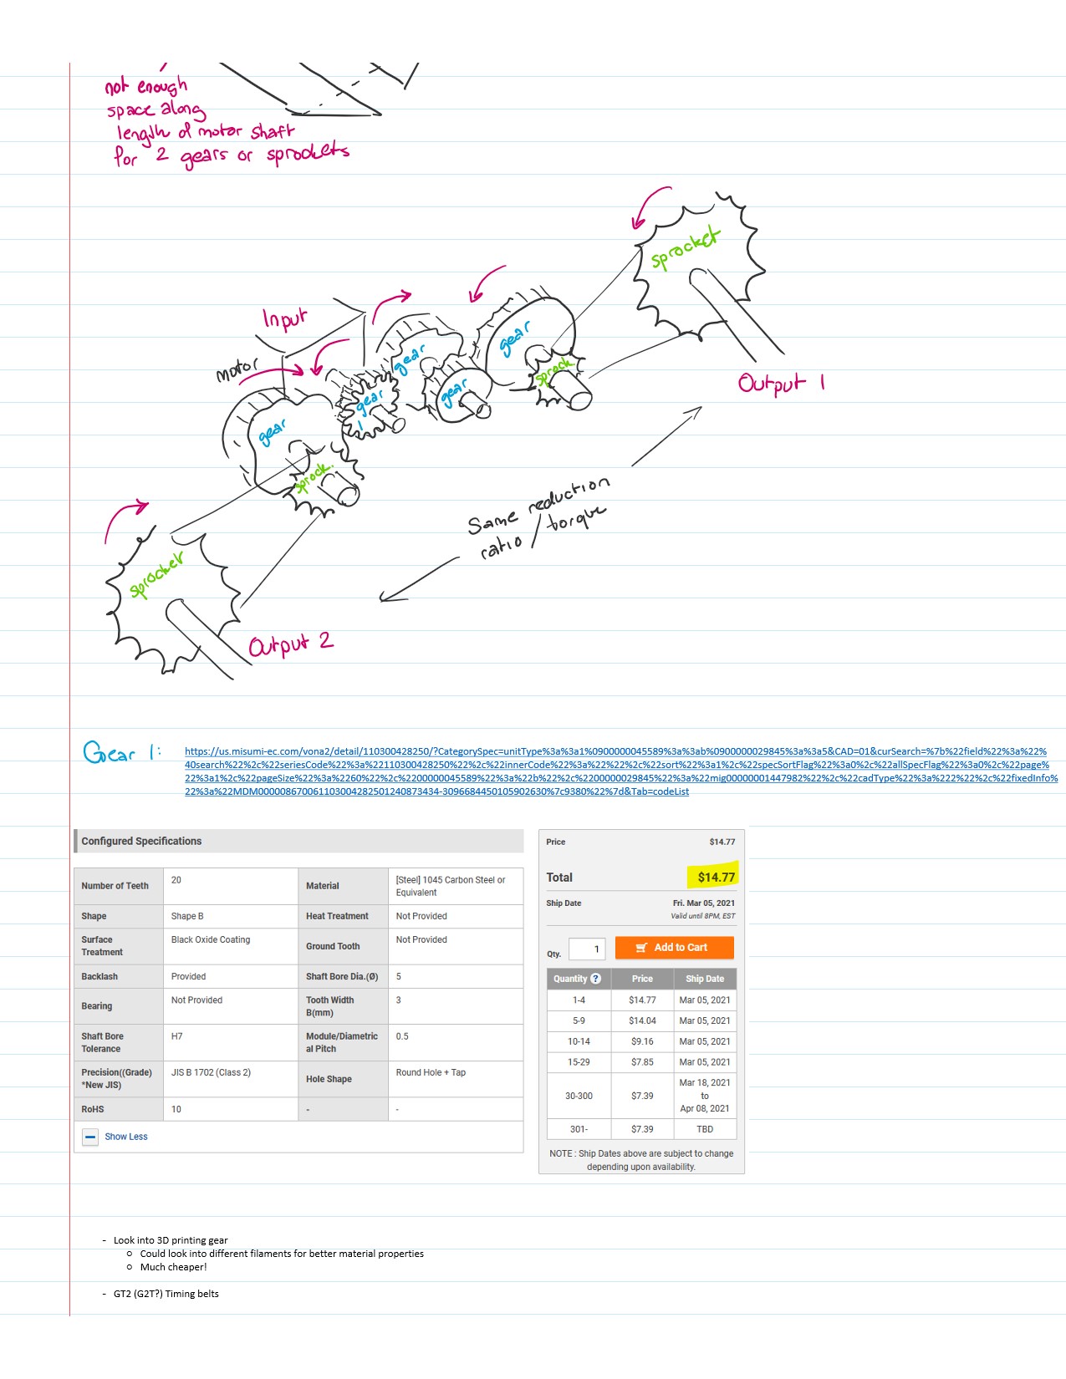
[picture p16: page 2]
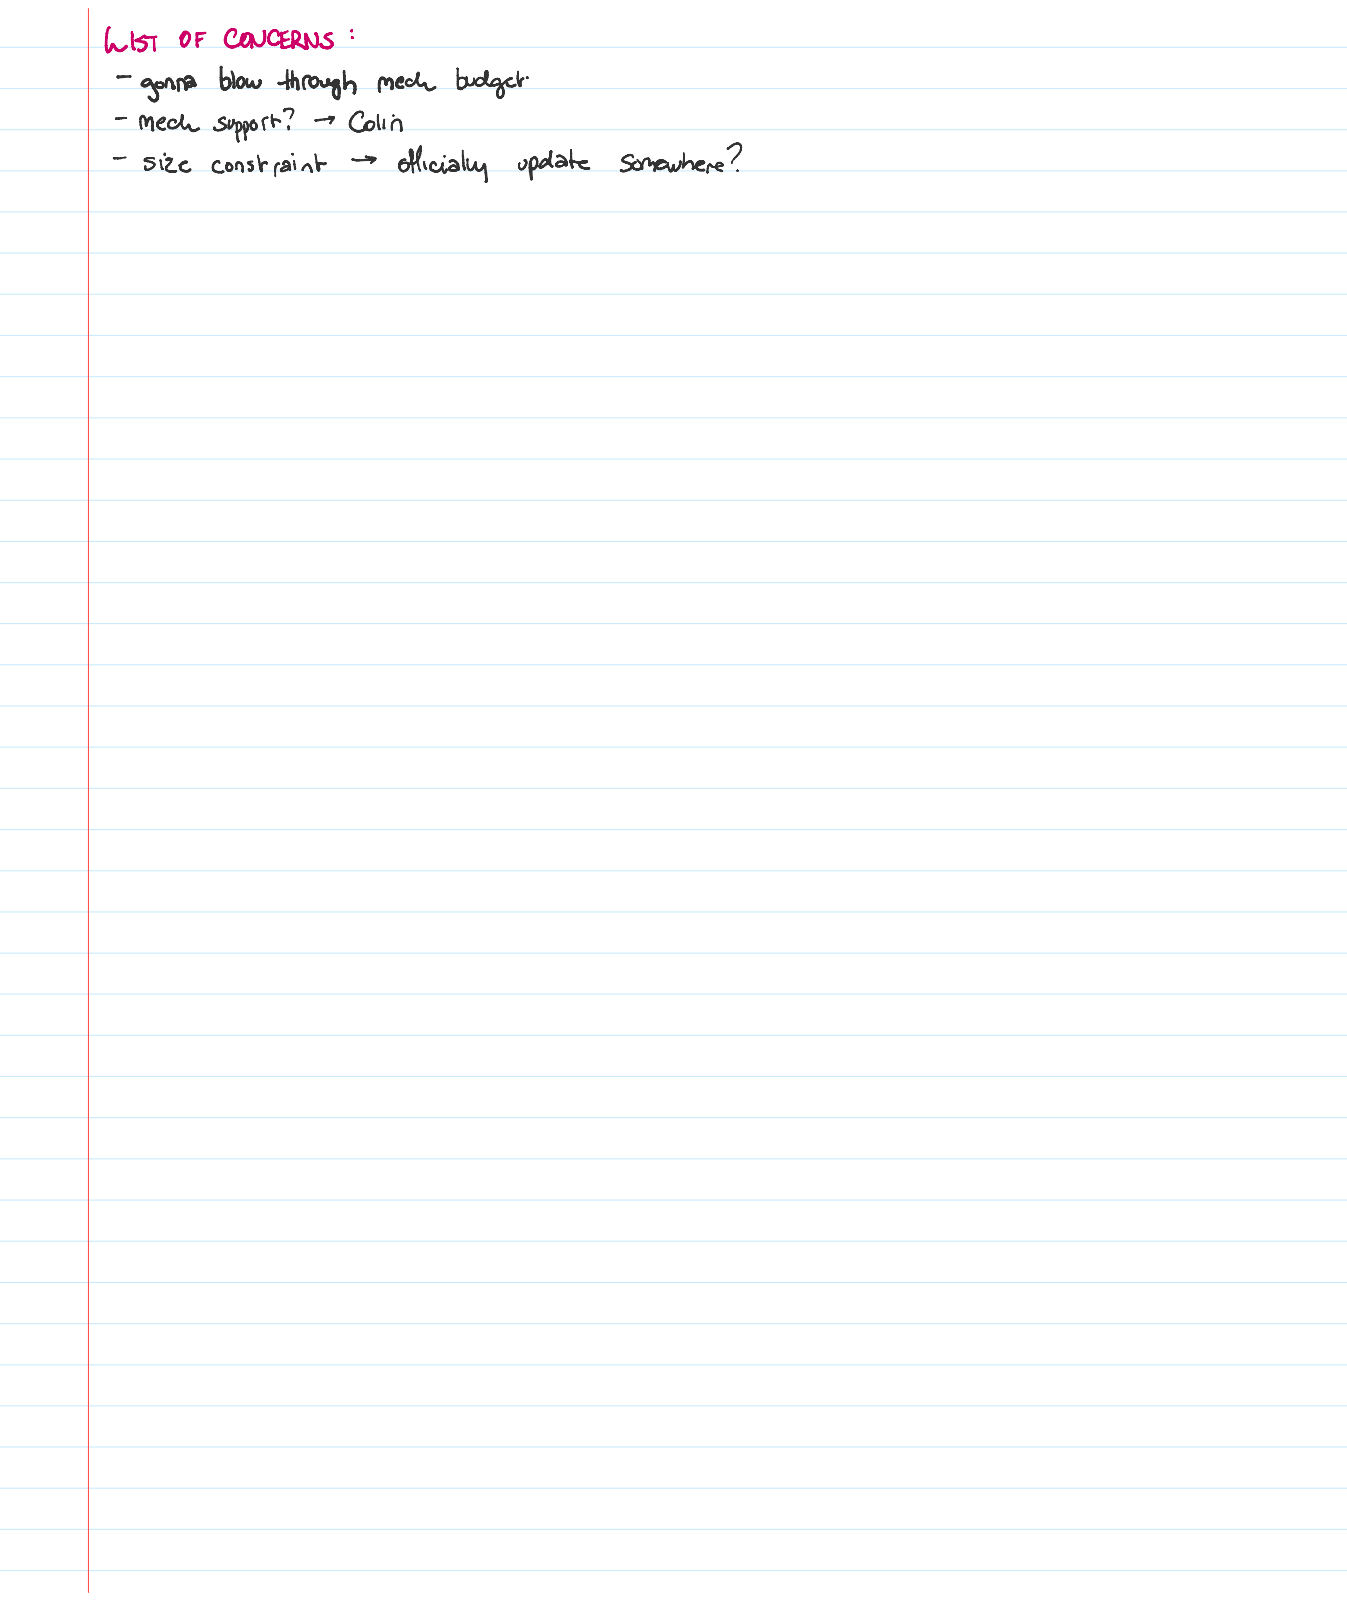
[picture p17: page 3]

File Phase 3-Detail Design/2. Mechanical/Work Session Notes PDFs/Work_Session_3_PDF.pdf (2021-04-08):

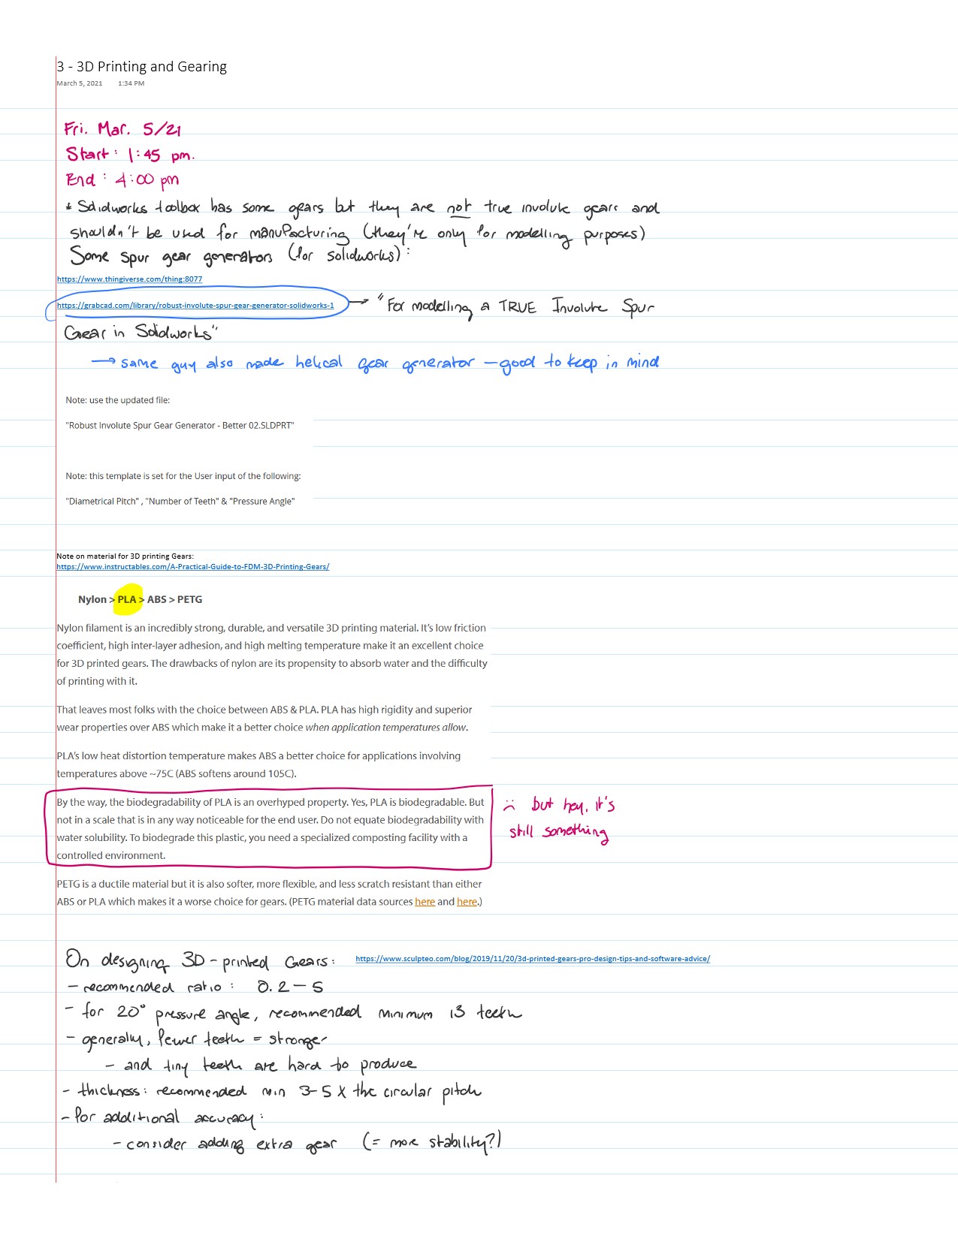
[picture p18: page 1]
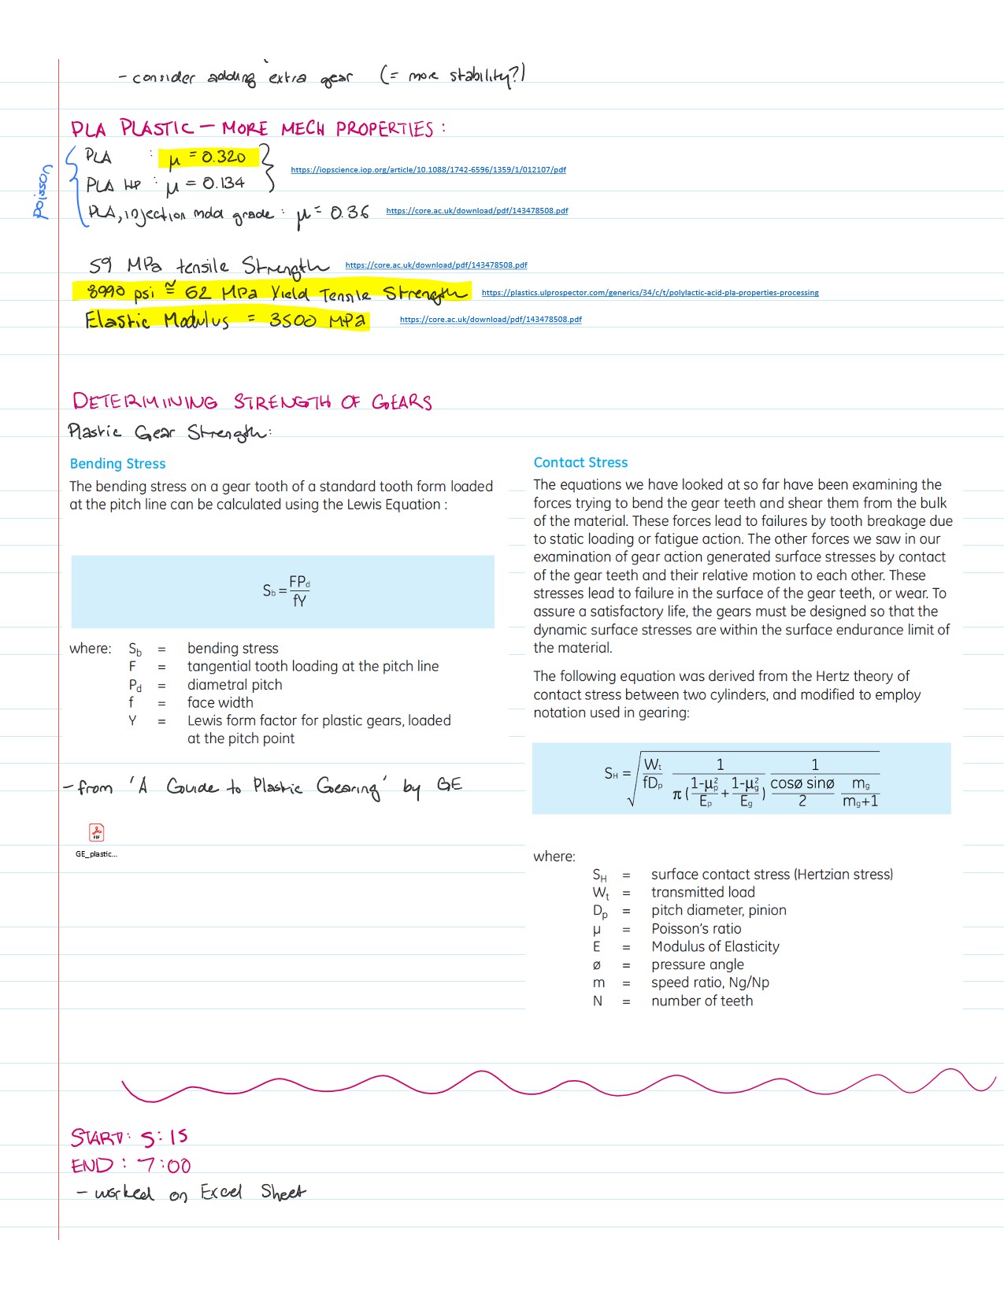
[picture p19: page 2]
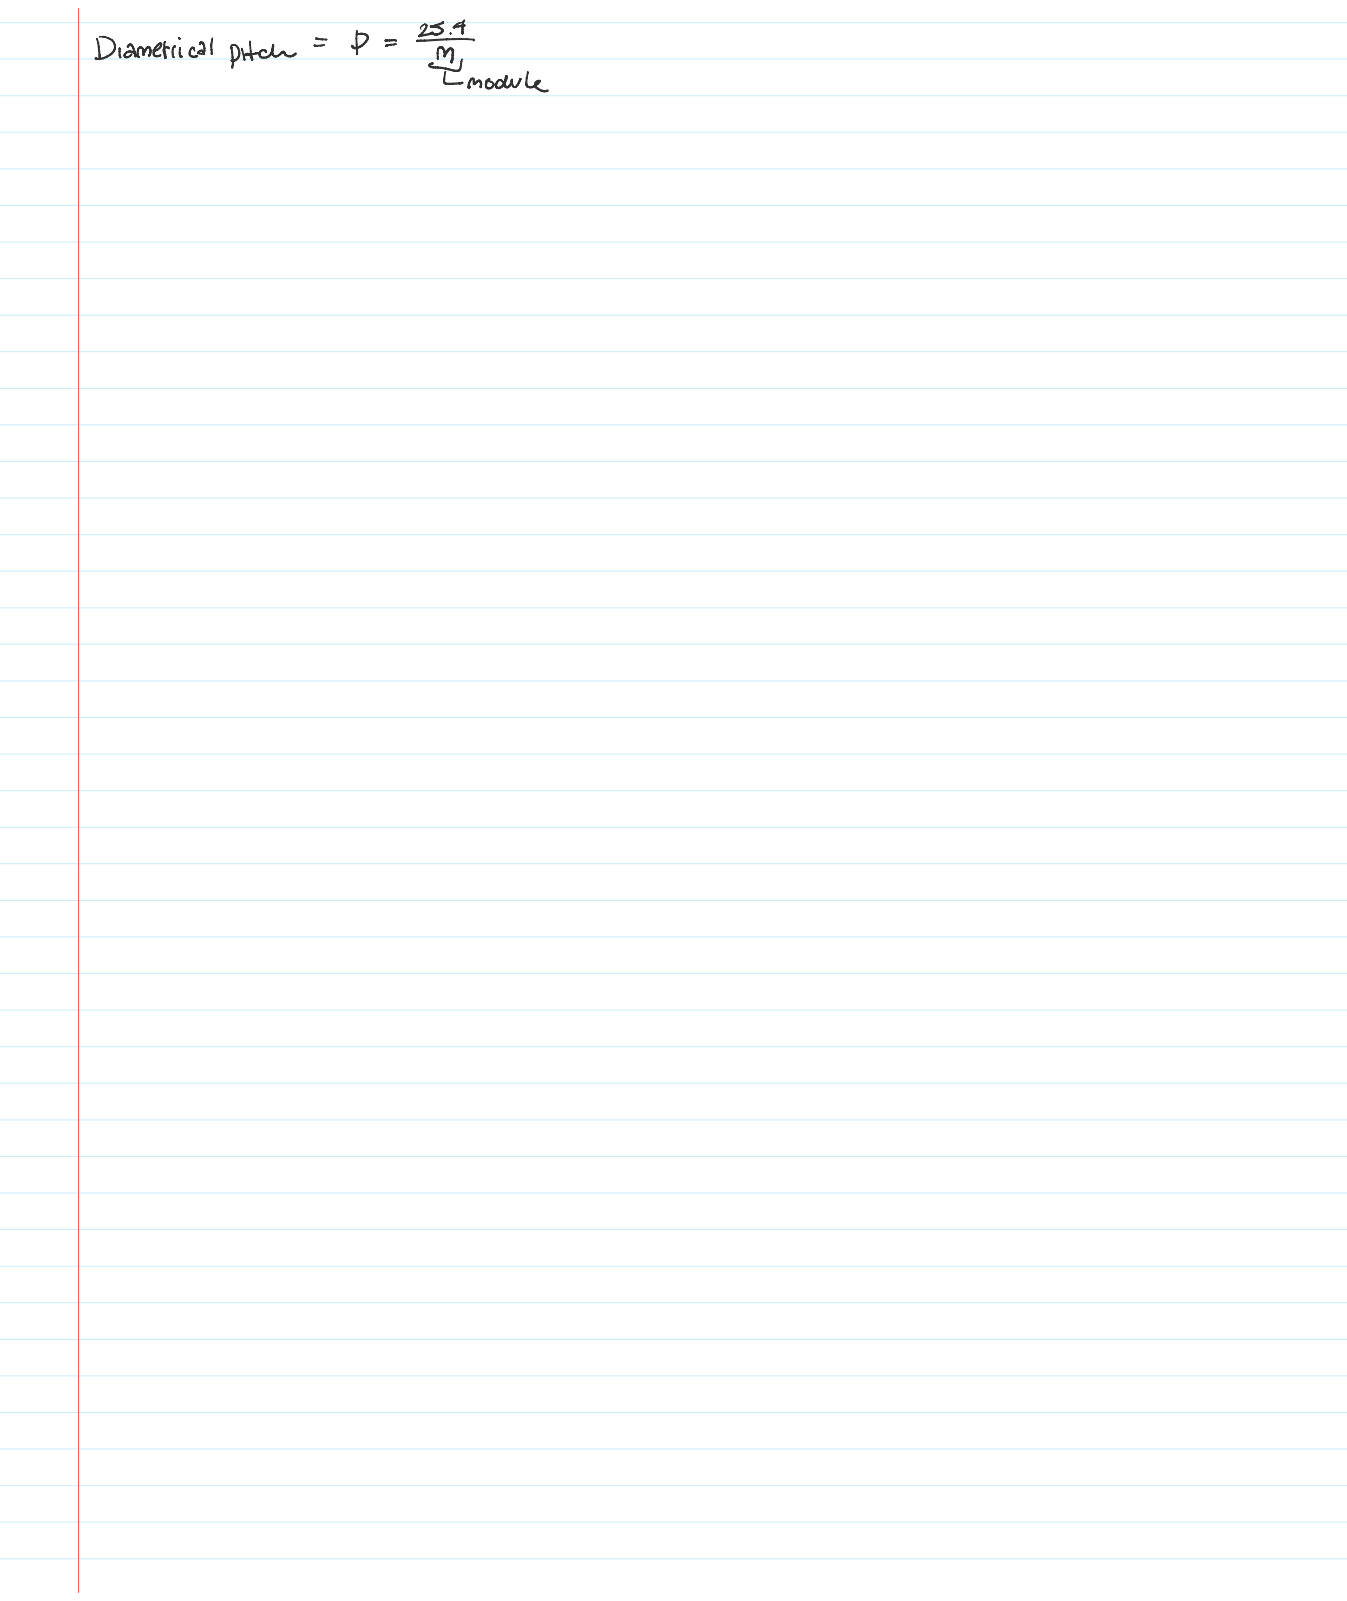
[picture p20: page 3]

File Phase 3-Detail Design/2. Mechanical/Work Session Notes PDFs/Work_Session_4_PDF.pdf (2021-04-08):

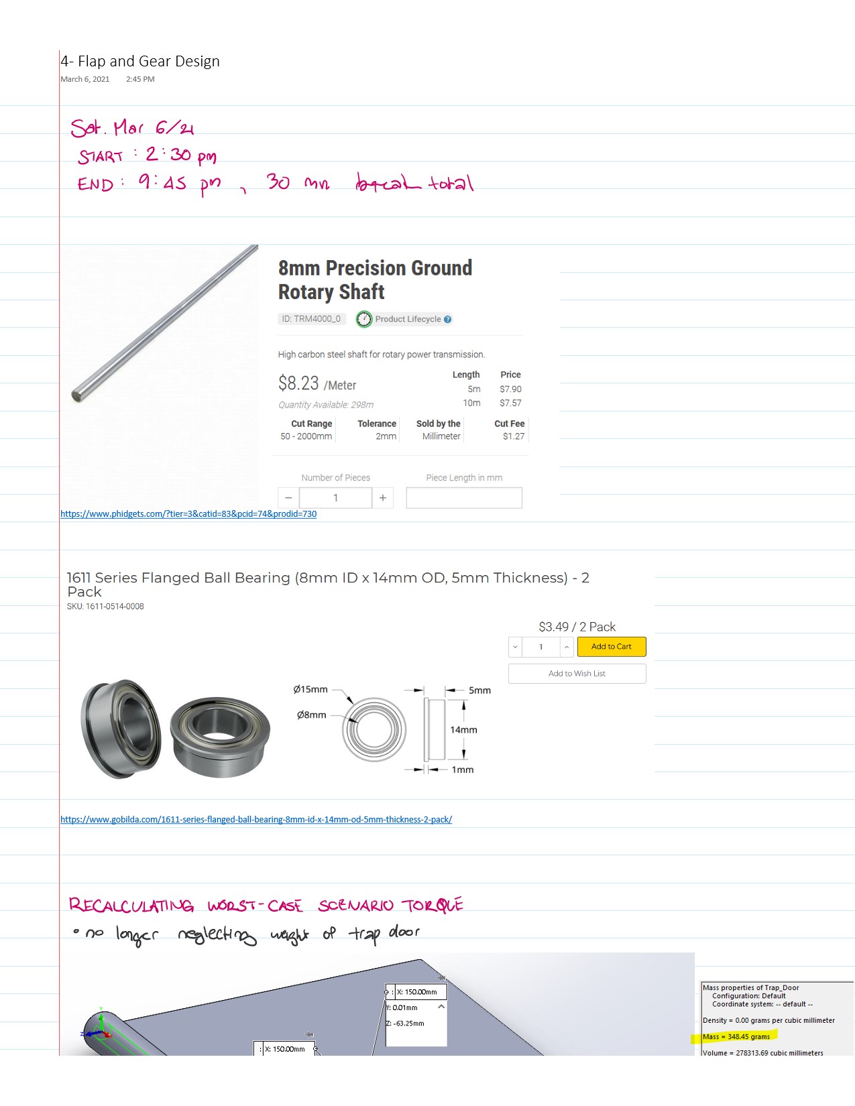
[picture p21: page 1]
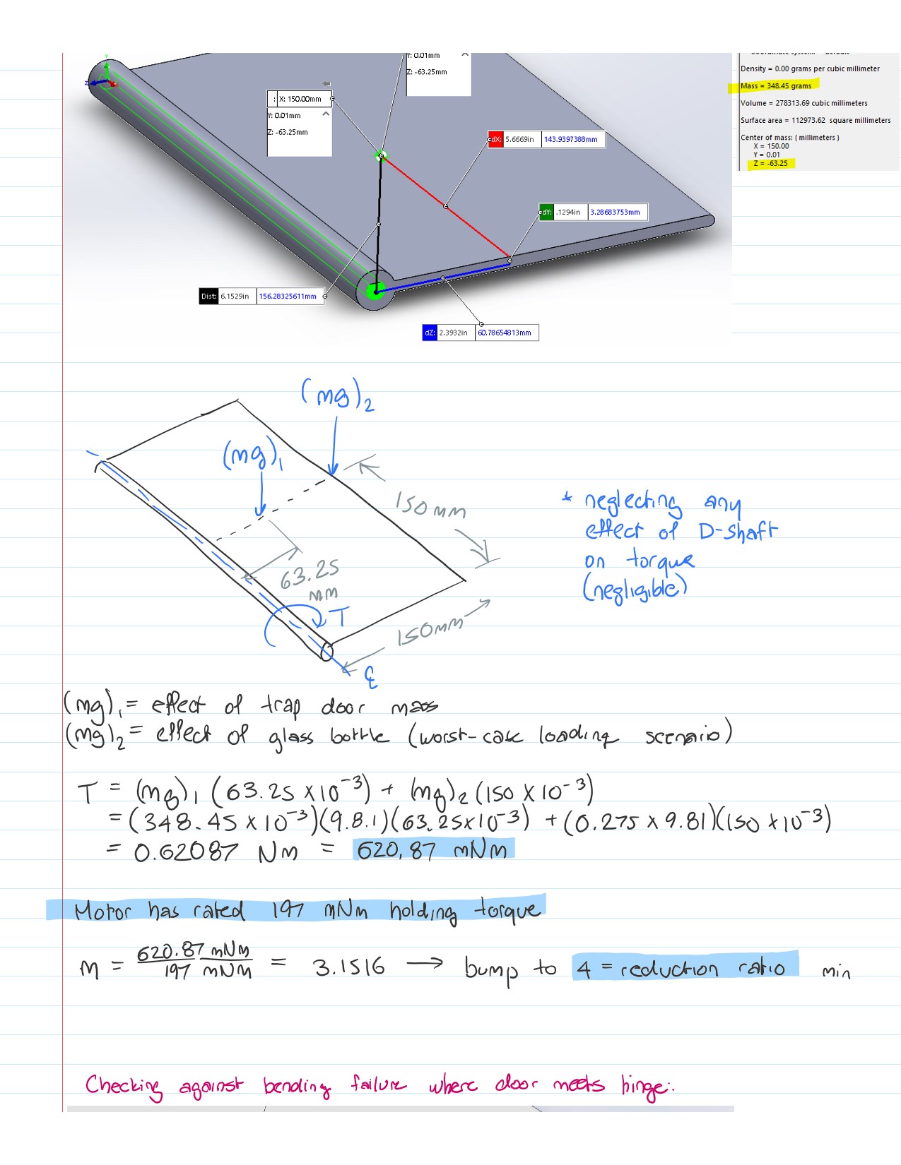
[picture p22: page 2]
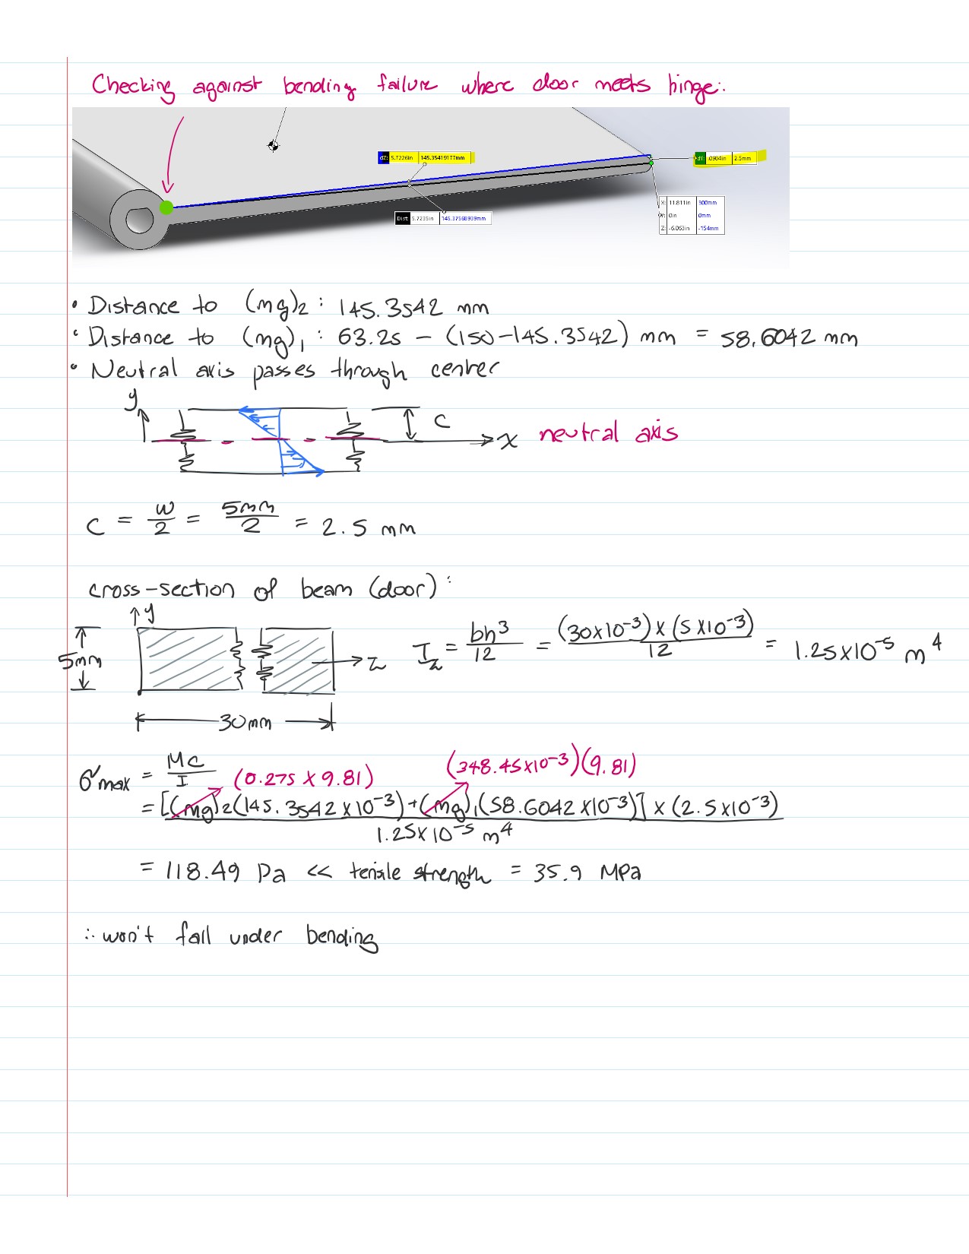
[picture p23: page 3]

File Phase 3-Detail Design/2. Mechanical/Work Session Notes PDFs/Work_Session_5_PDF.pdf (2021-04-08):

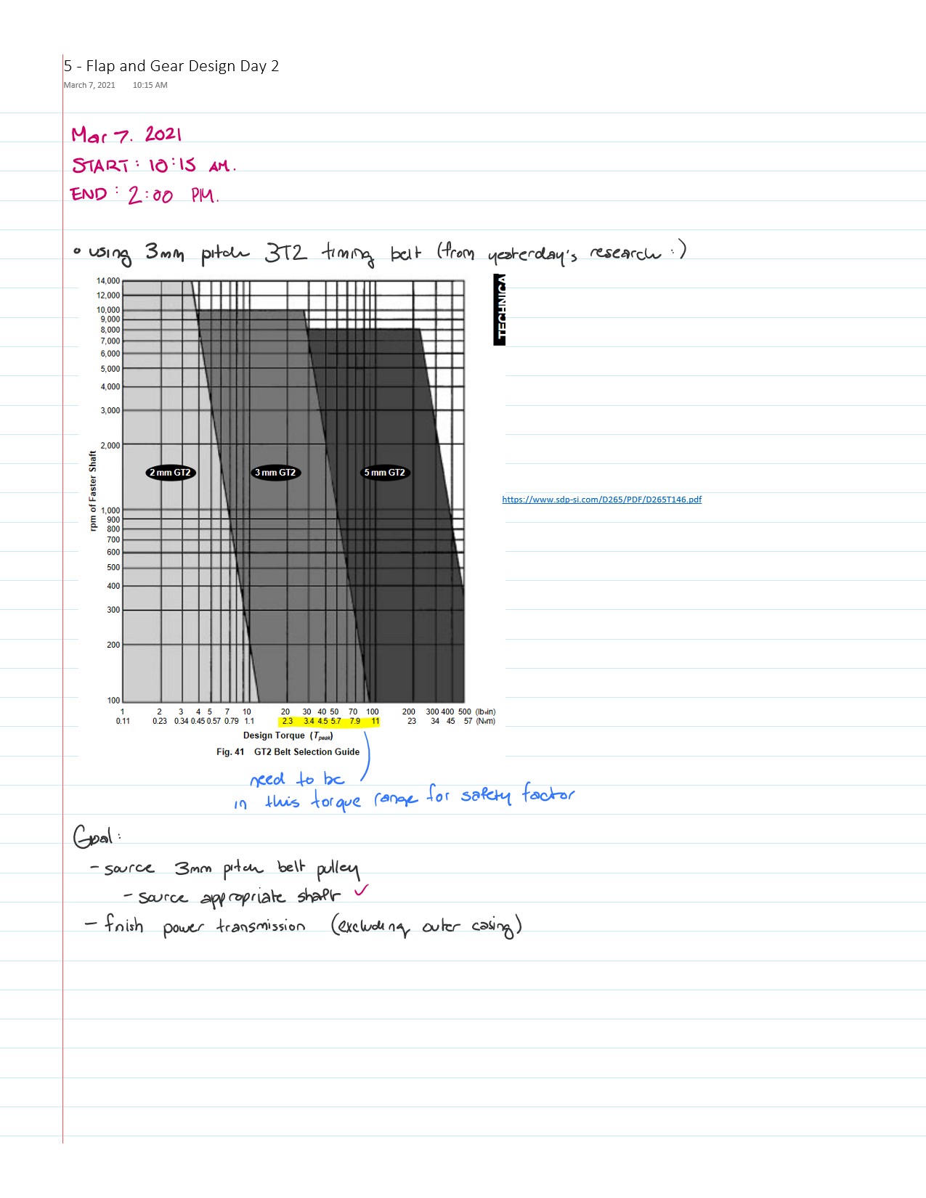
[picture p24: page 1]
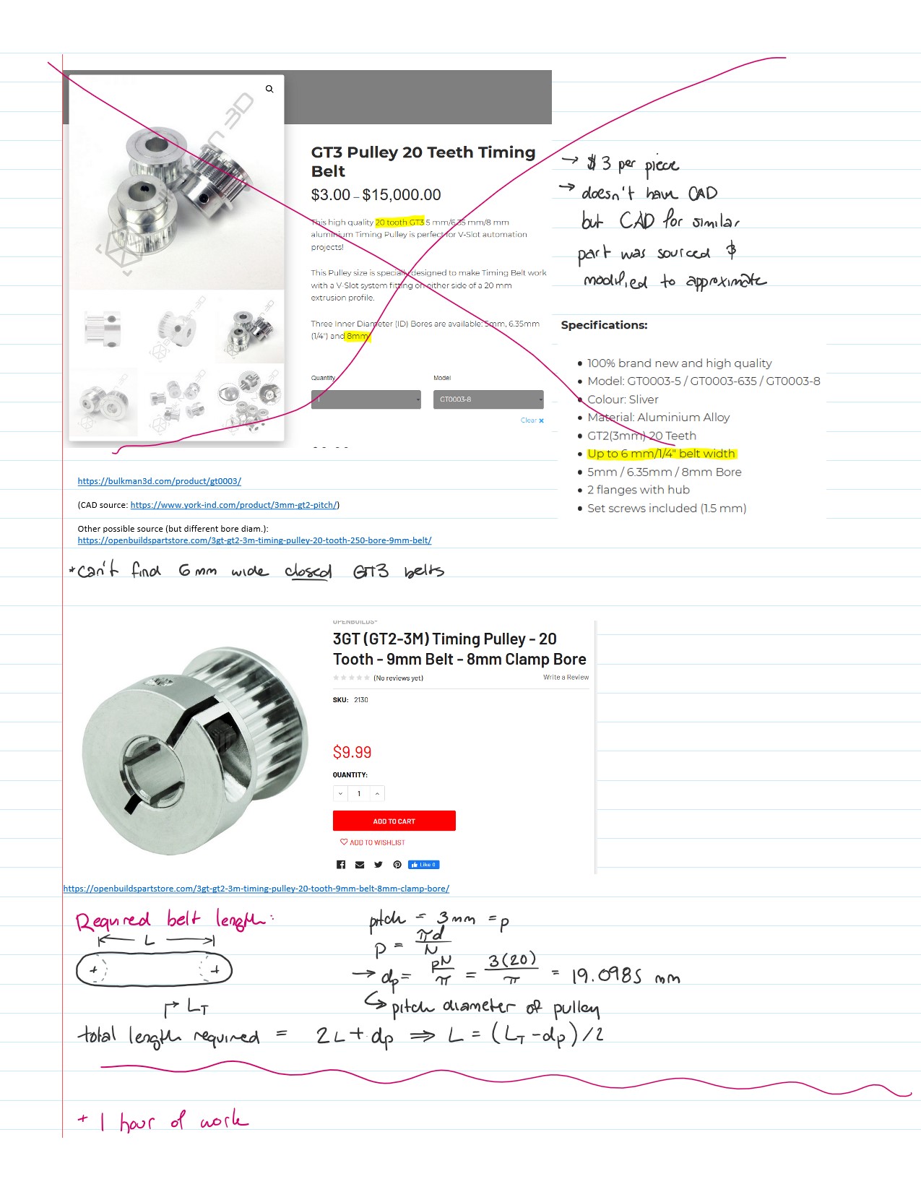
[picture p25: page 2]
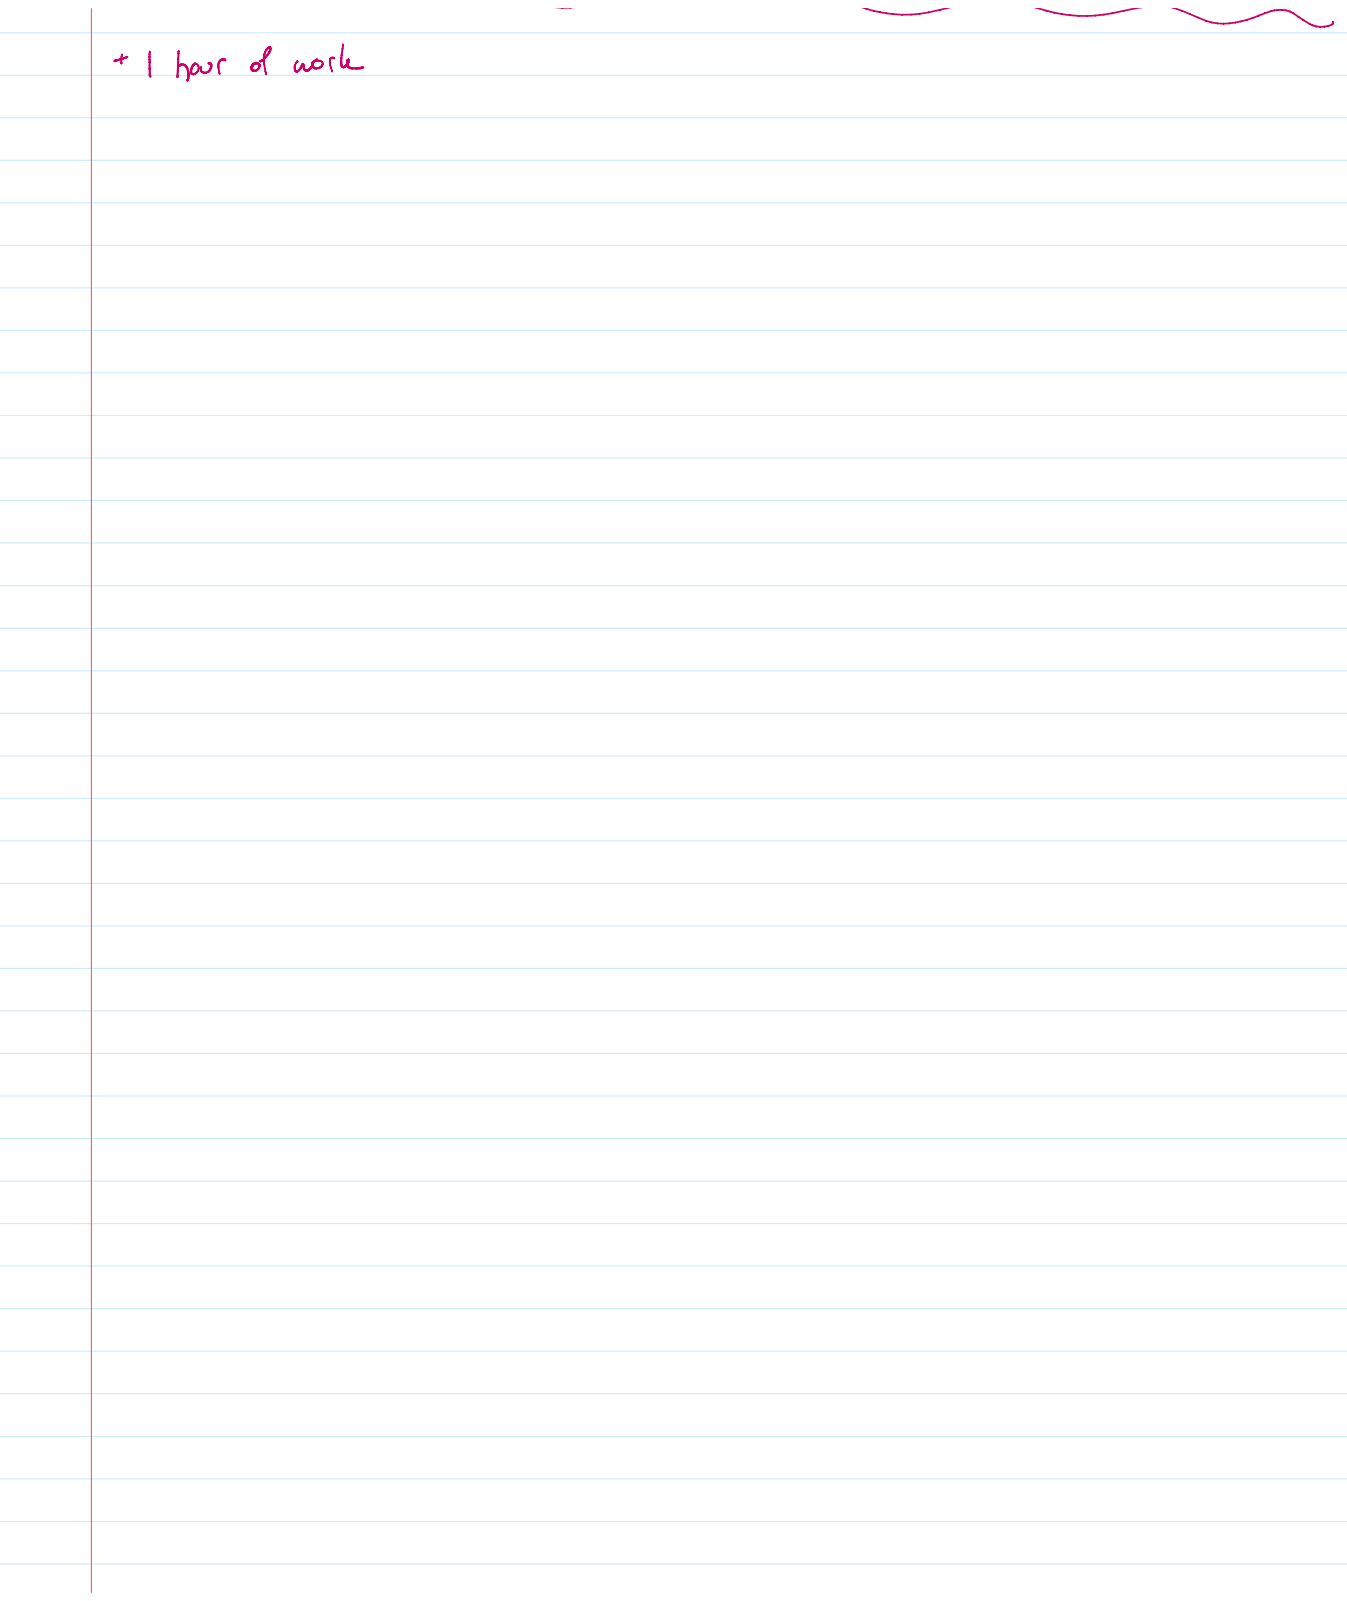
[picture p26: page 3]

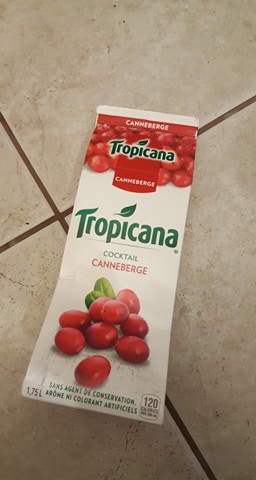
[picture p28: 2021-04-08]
Phase 3-Detail Design/4. Controls/Images/EG/Paper-Containers/156465258_247847950271613_9107680291389402422_n.jpg

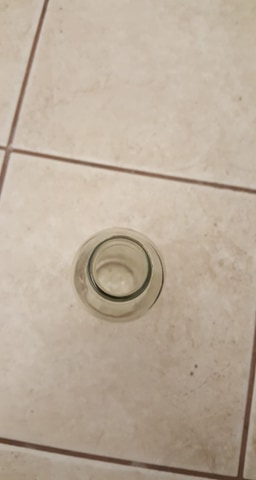
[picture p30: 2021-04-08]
Phase 3-Detail Design/4. Controls/Images/EG/Glass-Clear Bottles/156150728_1910058185816989_952591983705854807_n.jpg

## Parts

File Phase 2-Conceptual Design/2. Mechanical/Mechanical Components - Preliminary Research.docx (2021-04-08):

# Mechanical Components – Preliminary Research

The mechanical components make up the physical system including, but not necessarily limited to:

- Input of materials to be identified/sorted
- Output of identified/sorted materials
- Actuators involved in moving the material through the intermediate/identification stage

## 1. Factors to Consider First

### 1.1 Average Weight of Recyclables/Trash

How much weight does this system need to support/transport (aside from supporting functional components and housing)?

- Avg weight of plastic (single-use) waterbottle: 9.25 g [1]
- Avg weight of empty AT2 glass bottle (standard beer bottle): 275 g [2]
- Avg weight of empty pizza box: 153 g [3]
- Avg weight of empty soup can: 13.11 g [4]

Useful quick reference weights for some common recyclables: https://www.aspower.com/aspaweb/bids/RFP%20NO.%20ASPA14.1216%20ASPA%20AND%20PUBLIC%20JOINT%20VENTURE%20RECYCLING-Appendix%20A.pdf [4]

It is likely that glass bottles will be the heaviest materials that need to be transported. For the purpose of this preliminary research, I will assume that the largest mass of recyclables that needs to be moved at any moment does not exceed 500 g.

### 1.2 Gentleness of the System

At least in the region of Waterloo, broken glass is not recyclable [5]. This is to ensure the safety of the workers handling the recyclables [5]. For simplicity, I will assume that no broken glass is entering the system. However, because of potential safety concerns/recycling regulations, the system should also handle the materials with enough gentleness that no glass breaks during the identification/sorting process. This can affect which input/output/sorting mechanisms are viable, and details such as rpm in motor selection/control.

## 2. Component Research

### 2.1 Motors

Motor requirements will rely heavily on how the motor is being implemented (for linear translation, rotary, what other components is it working with, etc.) so this research will provide a general overview of some commonly available small electric motors.

For a mass of 1 kg at a distance of 15 cm (a rough worst-case scenario based on a large mass concentrated on the center of a 30 cm long motorized flap – this will be refined when an actual design/motor configuration is selected), we need a minimum torque of approximately:

T=0.5 kg ×9.81 m/s^2 ×0.15 m =0.73575 Nm=735.75 mNm

To keep prices moderate, this torque will have to be achieved with a speed reduction (gears).

Some sample DC motors:

Model Name | Brand | Speed (rpm) | Torque (Nm) | Power (W) | Unit Price | Source
22N28-216E.286 | Digi-Key | 10000 | 0.0084 | 3.8 | $64.98 | [6]
755-19175-C | Transmotec | 3900 | 0.0336 | 14 | $60.30 USD | [7]
775-9009F-C-CC | Transmotec | 18000 | 0.1026 | 194 | $61.30 USD | [8]

### 2.2 Linear Actuators

Below taken from [9].

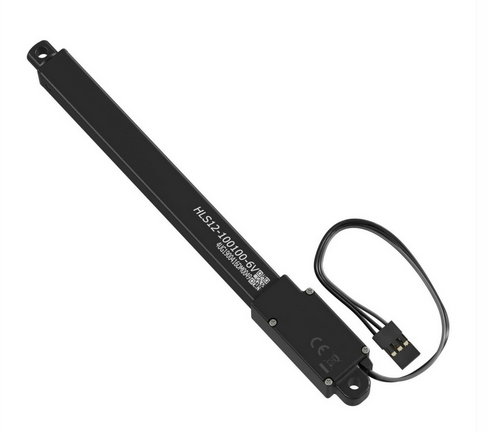
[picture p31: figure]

- 100 mm stroke
- $133.32 CAD
- Max force (lifted): Load = 4.2 kg, Speed = 3.2 mm/s

Below taken from [10].

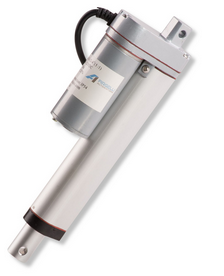
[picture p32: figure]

- 24” stroke
- $146.65 CAD
- Force: 150 lbs

Below taken from [11].

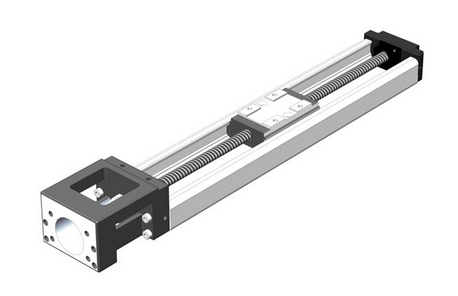
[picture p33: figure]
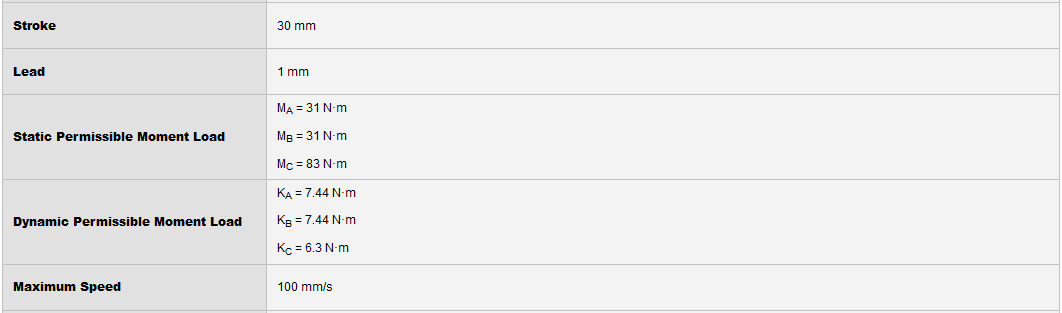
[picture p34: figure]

- $602.65
  - Expensive, but we can use the same principles and make our own

### 2.3 Pneumatic/Hydraulic Actuators

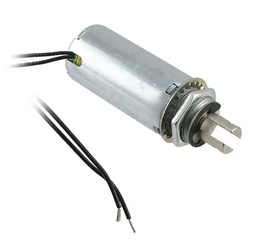
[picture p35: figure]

- Pneumatic
- $52.27
- 19.05 mm stroke length
  - Likely way too small to be useful
  - Difficult to find reliable pricing for longer stroke lengths
- https://www.digikey.ca/en/products/detail/pontiac-coil-inc/F0483A/668315
- Hydraulic
- $75.91
- 6 inch (?) stroke length
- https://www.baileyhydraulics.com/Cylinders-for-Snowplow-Applications-Double-Ports

### 2.4 Grabbers

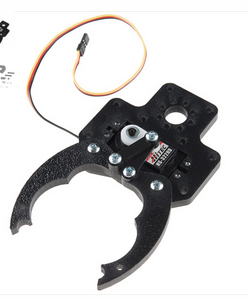
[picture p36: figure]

- $13.99
- https://www.robotshop.com/ca/en/actobotics-horizontal-standard-gripper-kit-a.html
- Can grab items up to 4.20” wide

### 2.5 Other

An assortment of various power transmission components we can make use of.

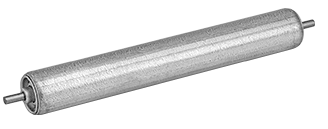
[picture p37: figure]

¾” Diameter conveyor roller

- $8 each
- 30 lbs capacity
- https://www.mcmaster.com/2278T11/

# Quick References

[1] | https://www.recyclingtoday.com/article/water-bottle-weight-decreases-recycled-content-increases/
[2] | https://unitedbottles.com/product/canadian-isb-341-ml-at2p
[3] | https://www.maarslet-pizza.dk/w-pizza/weight-of-pizza-box.html
[4] | https://www.aspower.com/aspaweb/bids/RFP%20NO.%20ASPA14.1216%20ASPA%20AND%20PUBLIC %20JOINT%20VENTURE%20RECYCLING-Appendix%20A.pdf
[5] | https://www.regionofwaterloo.ca/en/living-here/my-waste-app.aspx#!rc-cpage=487148
[6] | https://www.digikey.ca/en/products/detail/portescap/22N28-216E-286/5232871
[7] | https://transmotec.com/product/755-19175-C/
[8] | https://transmotec.com/product/775-9009F-C-CC/
[9] | https://www.robotshop.com/ca/en/hitec-hls12-series-6v-linear-actuator-100mm-1001.html
[10] | https://www.robotshop.com/ca/en/firgelli-24-150lb-linear-actuator.html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
[11] | https://catalog.orientalmotor.com/item/linear-actuators-linear-slides-only/shop-thk-linear-slides-actuators/kr2001a-0030-0-01a0

Emily Studzinski

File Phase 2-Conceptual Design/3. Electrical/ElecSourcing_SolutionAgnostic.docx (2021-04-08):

The parts sourced here are in reference to the MORPHOLOGICAL CHART and the various sensors, actuators, and ‘brains’ required for the project. Note that since no specific solution has been selected yet (need exactly this research into feasibility of various parts) each of the researched parts of the design below are solution agnostic and are intended to provide insight into what is possible, rather than exactly what will be done.

# 1. Board

## 1.1 System Brain

- Arduino
  - Website: arduino.cc
  - Specific Possibilities
    - Nano
      - Smallest Arduino board
      - No DC power jack, only pin
      - Mini-B cable required to program
    - Nano Every
      - Same as nano, more powerful processor
      - More program memory than Nano, Uno, etc.
      - Micro-USB cable required to program
      - Cheapest option
    - Uno Rev 3
      - Most used in family
      - Well documented
      - USB-B cable required to program
    - Leonardo
      - Like Uno
      - Built-in USB communication – no need for secondary processor
      - Virtual (CDC) serial/COM port
    - Mega 2560 Rev 3
      - 54 digital pins, 16 analog ins, 4 serial ports
      - Higher $
    - Due
      - 54 digital pins, 12 analog in, 2 DAC, 2 CAN
      - “For powerful larger scale Arduino projects”
      - First Arduino based on 32-bit ARM core microcontroller
      - 3.3V only
      - Higher $
      - Faster clock
    - Micro
      - Micro-USB cable required to program
      - Is to the Leonardo as the Nano is to the Uno
    - Etc. - those listed so far should encompass any/all needs for the system, but if something different is required of the ‘brain’ of the system there’s more available on the website and/or look for shields
  - Comparison of popular Arduino boards: https://maker.pro/arduino/tutorial/a-comparison-of-popular-arduino-boards
    - Uno
      - Pin header arrangement rapidly becoming industry standard
      - Power jack + Vin
      - 5V & 3.3V
      - Relatively small dimensions
    - Nano
      - Uno shrunk to small profile – weight and space reduction
      - Cannot connect to shields
      - Useful for breadboard prototyping or PCBs
      - Cheap
    - Due
      - ARM core
      - Powerful
      - 3.3V, else irreparable damage
      - No on-board EEPROM
      - Expensive
      - Pin-compatible with standard Arduino shields
      - Software compatibility not guaranteed
      - Large
    - Mega
      - Software compatibility not guaranteed
      - Large
      - 5V
    - In general:
      - Excellent support to all boards
      - Common architecture, language, IDE – few device-specific traps
      - Easily transfer code to diff boards
      - Deciding factor for each project: hardware and cost
      - Nano smallest, Uno medium, Mega and Due large
      - Due best processing power
      - Due and Mega have plenty of GPIO
      - Due has best analog comatibility: 12 analog in and 2 analog out
  - Features/Complications
    - Simple/rapid implementation
    - Simple/rapid programming
    - Very limited memory
    - Open Source
    - More complex tasks are difficult to accomplish
    - Due alone is 32 bit, all others 8 bit
- Raspberry Pi
  - Specific Possibilities - mostly range from RPi1 thru RPi4, A and B models. Comparison: https://socialcompare.com/en/comparison/raspberrypi-models-comparison
    - Pico
      - Cheap (4USD)
      - Weaker core
      - Micro-USB, 2xSPI, 26 GPIO pins, 2xUART serial
      - No wireless connectivity on-board
      - Small
      - Not a full computer
      - Similar to Arduino Nano
    - Zero
      - Smallest and cheapest true RPi (5USD)
      - Still a full computer
      - More wired options than Pico
      - No wireless connectivity on-board
      - Lowest current draw RPi
      - Least capable Pi besides Pico
    - Zero W
      - Cheap (10USD)
      - Relatively low current draw
      - RPi Zero with WiFi and Bluetooth
    - Zero WH
      - Cheap (15 USD)
      - RPi Zero W with header already soldered
    - Others
      - Higher generation number is more powerful
      - Higher generation number is more expensive, for the most part
      - Model A usually smaller, less RAM than Model B
  - Features/Complications
    - Supports complex software – can host an operating system
    - Various ports to interact with – a general solution
    - Implies more difficult software implementation
    - Basically, a full computer on a small board
    - Variety of ports available
- Direct Implementation of a microcontroller
  - Specific Possibilities
    - ATMEL
    - STM
    - Microchip
  - Features/Complications
    - Much harder to implement – flash, finicky details, etc.
    - Higher flexibility – many different microcontrollers available (hence, none specifically researched; depends on the application itself)

## 1.2 Circuit Implementation

The circuits for the microcontroller to interface with sensors and actuators

- Printed Circuit Board
  - Specific Possibilities
    - https://www.pcbway.com/
      - Very cheap – as low as 5$/board? (CAD? USD?)
      - Chinese – not supporting Canadian business, long lead time
    - https://www.pcbgogo.com/
      - Very cheap – as low as 5$/board? (CAD? USD?)
      - Chinese – not supporting Canadian business, long lead time
    - https://oshpark.com/#services
      - Manufactured in USA
      - 3 copies for 5$/square inch (likely USD) ships in 9-12 days
      - 3 copies for 10$/square inch (likely USD) ships in 4-5 business days
      - Volume discount if buying in bulk
    - MyRO PCB http://www.myropcb.com/online-quote/pcb-production-quote/
      - Canadian (Ottawa)
      - Standard PCB order: 20$ (likely CAD?), 5PCBs, 2 layer, 4x4 inch, 6 day lead time
    - Bittele
      - I think my company used them for a board that I designed on a work term
    - Various other Chinese manufacturers (e.g. jlcpcb) – there are also North American options; selection will probably depend on timeline (shipping) and cost preference
  - Features/Complications
    - Need supplier
    - Not DIY and therefore less accessible to the consumer
    - Contained, guaranteed working circuit (if design is good)
- Breadboard
  - Various sizes available
  - Features/Complications
    - Extremely flexible
    - Extremely accessible to the layperson
    - Chance user could damage electrical components by making bad circuits
    - Ambiguous power rating
    - Parasitic capacitances, inductances
    - Widely available
- Perf board
  - Various sizes available
  - Like breadboard, but requires soldering – better anchoring
  - Features/Complications
    - Flexible
    - Accessible to anyone who can use a soldering iron
    - Chance user could damage electrical components by making bad circuits

# 2. Sensors

## 2.1 Light

- Laser
  - Eye safety concerns
  - Good at distance
  - Lightweight
  - Single point measurement
- Interrupted Beam
  - Simple premise
  - Boolean logic
  - Must align – any bump out of position is no bueno
- Image Recognition
  - All logic in software
  - Less dependent on sensor itself as treatment of data
  - Need better controller to manage – may be pricier
- Photoresistor
  - Very cheap
  - Analog
  - Medium sensitivity
- Photodiode
  - Very cheap
  - Fast
  - Less sensitive than phototransistor
- Phototransistor
  - Cheap
  - Slower than photodiode
  - Very sensitive

## 2.2 Magnetic

- Hall Effect
  - Lower measuring accuracy than fluxgate magnetometers or magnetoresistance-based sensors
  - Drift, need compensation
  - Does not suffer mechanical switch problems, if used as a switch
  - For magnetic-field-strength measurement – can measure wide range of fields, sign and amplitude

## 2.3 Electrical

- Conductivity
- Capacitive
  - Detect or measure anything that is conductive or has a dielectric different from air
    - Mutual capacitance: object alters coupling of electrodes
    - Self-capacitance: object loads the sensor or increases parasitic capacitance
- Inductive
  - Current induced when magnetic field changes (or vice versa)

## 2.4 Sonic

- Ultrasonic & accelerometer
  - Distance to object
  - Cost varies with quality

## 2.5 Interface

- Lights and buttons
  - Very cheap
  - Easy electrical implementation
  - Simple commands
  - Low-level
- Touchscreen
  - Varied qualities/costs available
  - Customisable display
  - Combined input/output
- LCD & buttons
  - Cheap
  - Customisable display
  - Electronics and software simple, low-level
- IOT+App/Website
  - Integrated solution
- Voice Commands/Speaker
  - Accessibility
  - Much software work required
  - Sonic I/O electronically simple
  - Can be cheap or expensive depending on I/O quality required (out usually simpler than in)
- Gesture Control
  - Accessibility
  - Much software work required

# 3. Actuators

## 3.1 Motors

Need to know more about physical dimensions, required power, etc. Point is, there are a variety of motors out there for any actuating need, but they depend on other design aspects

I don’t feel comfortable discussing various primarily-mechanical actuators at this time

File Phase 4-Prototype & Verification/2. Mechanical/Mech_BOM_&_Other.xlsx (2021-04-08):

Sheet: Rev_1
Item # | Part # | Source | Description | Unit Price (CAD)* | Quantity | Total Price | Unit Weight (g) | Total Weight (g) | Link
Intermediate Stage
1 | FILAMENT |  | 3D Printed Components |  | 1 | $0.00 | 2074.403969 | 2074.403969
2 | 1528-1062-ND | DigiKey | Stepper Motor | $19.02 | 1 | $19.02 | 200.03 | 200.03 | https://www.digikey.ca/en/products/detail/adafruit-industries-llc/324/5022791
3 | TRM4000_0 | Phidgets | 8mm Rotary Shaft*** | $6.50 | 0.95 | $6.18 | 363.575 | 345.39625 | https://www.phidgets.com/?tier=3&catid=83&pcid=74&prodid=730
4 | 1611-0514-0008 | gobilda | 8mm ID Ball Bearing, 2 pack | $4.36 | 4 | $17.45 | 6 | 24 | https://www.gobilda.com/1611-series-flanged-ball-bearing-8mm-id-x-14mm-od-5mm-thickness-2-pack/
5 | 217-5887 or 217-5888 | VEX Robotics | GT3 Timing Belt | $8.49 | 1 | $8.49 |  | Negligible | https://www.vexrobotics.com/gt2-timingbelts.html?___store=vexroboticsca&___from_store=vexrobotics
6 | 2130 | openbuilds | GT3 Timing Pulley, 20T, 9mm belt | $12.49 | 2 | $24.98 |  | Negligible | https://openbuildspartstore.com/3gt-gt2-3m-timing-pulley-20-tooth-9mm-belt-8mm-clamp-bore/
7 | 90592A095 | McMaster-Carr | M5x0.8mm Hex Nut | $0.02 | 16 | $0.35 | 1.21 | 19.36 | https://www.mcmaster.com/90592A095/
8 | 91290A231 | McMaster-Carr | M5x0.8mm, 15mm long socket head | $0.26 | 16 | $4.14 | 3.68 | 58.88 | https://www.mcmaster.com/91290A231/
9 | 91290A572 | McMaster-Carr | M3x0.5mm, 15mm long socket head | $0.25 | 12 | $3.00 | 1.12 | 13.44 | https://www.mcmaster.com/91290A572/
10 | 95947A502 | McMaster-Carr | M3x0.5mm standoff, 50mm long | $2.23 | 4 | $8.90 | 2.17 | 8.68 | https://www.mcmaster.com/95947a502
11 | 95947A018 | McMaster-Carr | M3x0.5mm standoff, 25mm long | $1.35 | 2 | $2.70 | 0.8 | 1.6 | https://www.mcmaster.com/95947A018/
12 | 92605A652 | McMaster-Carr | M3x0.5mm set screw | $0.33 | 5 | $1.66 | 0.244 | 1.22 | https://www.mcmaster.com/92605A652/
Output Stage
1 | FILAMENT |  | 3D Printed Components |  | 1 | $0.00 | 1809.513459 | 1809.513459
2 | 1528-1062-ND | DigiKey | Stepper Motor | $19.02 | 1 | $19.02 | 200.03 | 200.03 | https://www.digikey.ca/en/products/detail/adafruit-industries-llc/324/5022791
3 | 91290A231 | McMaster-Carr | M5x0.8mm, 15mm long socket head | $0.26 | 10 | $2.58 | 3.68 | 36.8 | https://www.mcmaster.com/91290A231/
4 | 90592A095 | McMaster-Carr | M5x0.8mm Hex Nut | $0.02 | 10 | $0.22 | 1.21 | 12.1 | https://www.mcmaster.com/90592A095/
5 | 90751A111 | McMaster-Carr | M3x0.35mm, 8mm long socket head | $0.12 | 4 | $0.46 | 0.84 | 3.36
 |  |  |  |  | Total | $119.15 |  | 4808.813678
 |  |  |  |  |  |  | Mass in kg: | 4.809
* before tax
** based on CAD - USD currency conversion rate on 03/19/21: $1 CAD = $0.80 USD
*** priced by the m, sold by the mm. "Quantity" is in m. "Unit Price" and "Unit Weight" are per m
For fasteners sold in packs, price for 1 unit was determined
USD -> CAD conversion rate: |  | 1.25

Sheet: Rev_2
Item # | Part # | Source | Description | Unit Price (CAD)* | Quantity | Total Price | Unit Weight (g) | Total Weight (g) | Link
Intermediate Stage
1 | Filament spool |  | 3D Printed Components | $20.00 | 1.28308 | $25.66 |  | 1283.08
2 | 1528-1062-ND | DigiKey | Stepper Motor | $19.02 | 1 | $19.02 | 200.03 | 200.03 | https://www.digikey.ca/en/products/detail/adafruit-industries-llc/324/5022791
3 | TRM4000_0 | Phidgets | 8mm Rotary Shaft*** | $6.50 | 0.95 | $6.18 | 363.575 | 345.39625 | https://www.phidgets.com/?tier=3&catid=83&pcid=74&prodid=730
4 | 1611-0514-0008 | gobilda | 8mm ID Ball Bearing, 2 pack | $4.36 | 4 | $17.45 | 6 | 24 | https://www.gobilda.com/1611-series-flanged-ball-bearing-8mm-id-x-14mm-od-5mm-thickness-2-pack/
5 | 217-5890 | VEX Robotics | GT3 Timing Belt, 110T | $10.99 | 1 | $10.99 |  | Negligible | https://www.vexrobotics.com/gt2-timingbelts.html?___store=vexroboticsca&___from_store=vexrobotics
6 | 2130 | openbuilds | GT3 Timing Pulley, 20T, 9mm belt | $12.49 | 2 | $24.98 |  | Negligible | https://openbuildspartstore.com/3gt-gt2-3m-timing-pulley-20-tooth-9mm-belt-8mm-clamp-bore/
7 | 90592A095 | McMaster-Carr | M5x0.8mm Hex Nut | $0.02 | 16 | $0.35 | 1.21 | 19.36 | https://www.mcmaster.com/90592A095/
8 | 91290A231 | McMaster-Carr | M5x0.8mm, 15mm long socket head | $0.26 | 16 | $4.14 | 3.68 | 58.88 | https://www.mcmaster.com/91290A231/
9 | 91290A572 | McMaster-Carr | M3x0.5mm, 15mm long socket head | $0.25 | 12 | $3.00 | 1.12 | 13.44 | https://www.mcmaster.com/91290A572/
10 | 95947A502 | McMaster-Carr | M3x0.5mm standoff, 50mm long | $2.23 | 4 | $8.90 | 2.17 | 8.68 | https://www.mcmaster.com/95947a502
11 | 95947A018 | McMaster-Carr | M3x0.5mm standoff, 25mm long | $1.35 | 2 | $2.70 | 0.8 | 1.6 | https://www.mcmaster.com/95947A018/
12 | 92605A652 | McMaster-Carr | M3x0.5mm set screw | $0.33 | 5 | $1.66 | 0.244 | 1.22 | https://www.mcmaster.com/92605A652/
13 | 92095A177 | McMaster-Carr | M3x0.5mm, 5mm long button head | $0.08 | 4 | $0.31 |  | Negligible | https://www.mcmaster.com/92095A177/
Output Stage
1 | Filament spool |  | 3D Printed Components | $20.00 | 1.1711 | $23.42 |  | 1171.1
2 | 1528-1062-ND | DigiKey | Stepper Motor | $19.02 | 1 | $19.02 | 200.03 | 200.03 | https://www.digikey.ca/en/products/detail/adafruit-industries-llc/324/5022791
3 | 91290A231 | McMaster-Carr | M5x0.8mm, 15mm long socket head | $0.26 | 10 | $2.58 | 3.68 | 36.8 | https://www.mcmaster.com/91290A231/
4 | 90592A095 | McMaster-Carr | M5x0.8mm Hex Nut | $0.02 | 10 | $0.22 | 1.21 | 12.1 | https://www.mcmaster.com/90592A095/
5 | 92095A177 | McMaster-Carr | M3x0.5mm, 5mm long button head | $0.08 | 4 | $0.31 |  | Negligible | https://www.mcmaster.com/92095A177/
 |  |  |  |  | Total | $170.88 |  | 3375.71625
 |  |  |  |  |  |  | Mass in kg: | 3.376
* before tax
** based on CAD - USD currency conversion rate on 03/19/21: $1 CAD = $0.80 USD
*** priced by the m, sold by the mm. "Quantity" is in m. "Unit Price" and "Unit Weight" are per m
For fasteners sold in packs, price for 1 unit was determined
PLA filament prices determined on sale price of ~ $20 per 1 kg spool: https://3dprintingcanada.com/collections/pla/products/transparent-red-2-85mm-pla-filament-1-kg
USD -> CAD conversion rate: |  | 1.25
Item # | Part # | Unit Weight (g) | Total Weight (g)
Intermediate Stage
1 | Filament spool |  | 1283.08
2 | 1528-1062-ND | 200.03 | 200.03
3 | TRM4000_0 | 363.575 | 345.39625
4 | 1611-0514-0008 | 6 | 24
5 | 217-5890 |  | Negligible
6 | 2130 |  | Negligible
7 | 90592A095 | 1.21 | 19.36
8 | 91290A231 | 3.68 | 58.88
9 | 91290A572 | 1.12 | 13.44
10 | 95947A502 | 2.17 | 8.68
11 | 95947A018 | 0.8 | 1.6
12 | 92605A652 | 0.244 | 1.22
13 | 92095A177 |  | Negligible
Output Stage
1 | Filament spool |  | 1171.1
2 | 1528-1062-ND | 200.03 | 200.03
3 | 91290A231 | 3.68 | 36.8
4 | 90592A095 | 1.21 | 12.1
5 | 92095A177 |  | Negligible
 |  |  | 3375.71625

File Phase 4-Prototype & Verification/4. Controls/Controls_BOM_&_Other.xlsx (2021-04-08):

Item # | Part # | Source | Description | Unit Price (CAD)* | Quantity | Total Price | Link
Intermediate Stage
1 | Jetson Nano 2GB | Amazon.ca | Jetson Nano 2GB - Used for Controller and AI Recognition | $80.16 | 1 | $80.16 | https://www.amazon.ca/NVIDIA-Jetson-Nano-Developer-945-13541-0000-000/dp/B08J157LHH
2 | Micro SD Card | Amazon.ca | 32GB Micro SD - Jetson Nano OS | $11.99 | 1 | $11.99 | https://www.amazon.ca/Sandisk-SDSQUAR-032G-GN6MA-Ultra-Micro-Adapter/dp/B073JWXGNT
3 | 5MP 1080P Camera | Amazon.ca | Camera for Jetson Nano - AI Recognition | $12.99 | 1 | $12.99 | https://www.amazon.ca/AuviPal-Megapixels-Raspberry-Camera-Module/dp/B07PQ63D2S
 |  |  |  |  | Total | $105.14

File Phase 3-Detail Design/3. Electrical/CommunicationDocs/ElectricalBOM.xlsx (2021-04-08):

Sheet: Schematic2
MTE 380 Group 3 - Electrical PCB Bill of Materials |  |  |  |  |  |  |  |  | *Note: this BOM only includes things mounted on the PCB - stepper motors, stepper motor drivers, mating connectors, wall wart & blade, will also be a part of the electrical cost
Item No. | Qty | References | Cost (per item) | Cost (total) | DigiKey Part No. | Description | Type | Package | *Note: all costs in CAD
1 | 1 | J1 | $0.62 | $0.62 | 839-54-00167-ND | CONN JACK R/A PCB 5.5X2.5MM | THT |  | *Note: bulk discounts not included
2 | 1 | F1 | $0.33 | $0.33 | 507-1888-1-ND | FUSE 7.0A 125VAC FAST 1206 | SMD | 1206 (3216M)
3 | 1 | U1 | $8.33 | $8.33 | 507-1384-ND | DC DC CONVERTER 0.59-5.1V 50W | THT | Header
4 | 1 | C1 | $0.82 | $0.82 | 490-16309-1-ND | CAP CER 47UF 16V X6S 1210 | SMD | 1210 (3225M)
5 | 1 | C2 | $0.43 | $0.43 | 478-13121-1-ND | CAP TANT 10UF 10% 10V 1206 | SMD | 1206 (3216M)
6 | 1 | C3 | $0.49 | $0.49 | 720-1807-1-ND | CAP CER 1UF 10V X7R 1206 | SMD | 1206 (3216M)
7 | 1 | R1 | $0.14 | $0.14 | P122414CT-ND | RES SMD 10K OHM 1% 1/20W 0201 | SMD | 0201 (0603M)
8 | 1 | R2 | $0.14 | $0.14 | YAG3080CT-ND | RES SMD 267 OHM 1% 1/16W 0402 | SMD | 0402 (1005M)
9 | 1 | Q1 | $0.71 | $0.71 | BSS806NEH6327XTSA1CT-ND | MOSFET N-CH 20V 2.3A SOT23-3 | SMD | SOT23-3
10 | 4 | J2,J22-24 | $0.43 | $1.72 | S7000-ND | CONN HDR 2POS 0.1 TIN PCB | THT | Header
11 | 1 | J3 | $2.65 | $2.65 | 1568-PRT-16764-ND | EXTENDED GPIO FEMALE HEADER - 2X | THT | Header
12 | 3 | F2-4 | $0.33 | $0.99 | 507-1883-1-ND | FUSE 3.0A 125VAC FAST 1206 | SMD | 1206 (3216M)
13 | 3 | J4, J6, J8 | $0.88 | $2.64 | S7008-ND | CONN HDR 10POS 0.1 TIN PCB | THT | Header
14 | 3 | J5, J7, J9 | $0.71 | $2.13 | S7004-ND | CONN HDR 6POS 0.1 TIN PCB | THT | Header
15 | 12 | J10-21 | $0.14 | $1.68 | A100452CT-ND | CONN QC TAB 0.250 SOLDER | THT
Total | 35 |  |  | $23.82

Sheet: OverallElecBOM
MTE 380 Group 3 - Electrical Bill of Materials |  |  |  |  |  | *Note: all costs in CAD
Item No. | Qty | Cost (per item) | Cost (total) | DigiKey Part No. | Description | *Note: bulk discounts not included
1 | 1 | $0.62 | $0.62 | 839-54-00167-ND | CONN JACK R/A PCB 5.5X2.5MM | *Note: only two motors and limit switches included in cost since that is what Mechanical currently requires
2 | 1 | $24.44 | $24.44 | 2103-ICM60-120-ND | AC/DC WALL MOUNT ADAPTER 12V 60W
3 | 1 | $1.72 | $1.72 | 2103-888992000-ND | US AC ADAPTER
4 | 1 | $0.33 | $0.33 | 507-1888-1-ND | FUSE 7.0A 125VAC FAST 1206
5 | 1 | $8.33 | $8.33 | 507-1384-ND | DC DC CONVERTER 0.59-5.1V 50W
6 | 1 | $0.82 | $0.82 | 490-16309-1-ND | CAP CER 47UF 16V X6S 1210
7 | 1 | $0.43 | $0.43 | 478-13121-1-ND | CAP TANT 10UF 10% 10V 1206
8 | 1 | $0.49 | $0.49 | 720-1807-1-ND | CAP CER 1UF 10V X7R 1206
9 | 1 | $0.14 | $0.14 | P122414CT-ND | RES SMD 10K OHM 1% 1/20W 0201
10 | 1 | $0.14 | $0.14 | YAG3080CT-ND | RES SMD 267 OHM 1% 1/16W 0402
11 | 1 | $0.71 | $0.71 | BSS806NEH6327XTSA1CT-ND | MOSFET N-CH 20V 2.3A SOT23-3
12 | 4 | $0.43 | $1.72 | S7000-ND | CONN HDR 2POS 0.1 TIN PCB
13 | 3 | $0.08 | $0.24 | S1012EC-02-ND | CONN HEADER VERT 2POS 2.54MM | male headers
14 | 1 | $0.88 | $0.88 | 2007-AB-FC01240-19700-8A1CT-ND | LIGHT STRIP W IP65 12V 3 LED/SEG | LED
15 | 2 | $0.58 | $1.16 | P10865S-ND | P10865S-ND | limit switches
16 | 1 | $2.65 | $2.65 | 1568-PRT-16764-ND | EXTENDED GPIO FEMALE HEADER - 2X
17 | 3 | $0.33 | $0.99 | 507-1883-1-ND | FUSE 3.0A 125VAC FAST 1206
18 | 3 | $0.88 | $2.64 | S7008-ND | CONN HDR 10POS 0.1 TIN PCB
19 | 3 | $0.71 | $2.13 | S7004-ND | CONN HDR 6POS 0.1 TIN PCB
20 | 2 | $0.26 | $0.52 | 2057-PH1-10-UA-ND | CONN HEADER VERT 10POS 2.54MM | 10 position male headers
21 | 2 | $0.16 | $0.32 | 2057-PH1-06-UA-ND | CONN HEADER VERT 6POS 2.54MM | 6 position male headers
22 | 2 | $6.72 | $13.44 | 1528-1212-ND | BREAKOUT TB6612 1.2A MOTOR DVR | Stepper motor drivers
23 | 12 | $0.14 | $1.68 | A100452CT-ND | CONN QC TAB 0.250 SOLDER
24 | 12 | $0.31 | $3.72 | A122972CT-ND | CONN QC RCPT 18-22AWG 0.250 | female QC tab
Total | 61 |  | $70.26

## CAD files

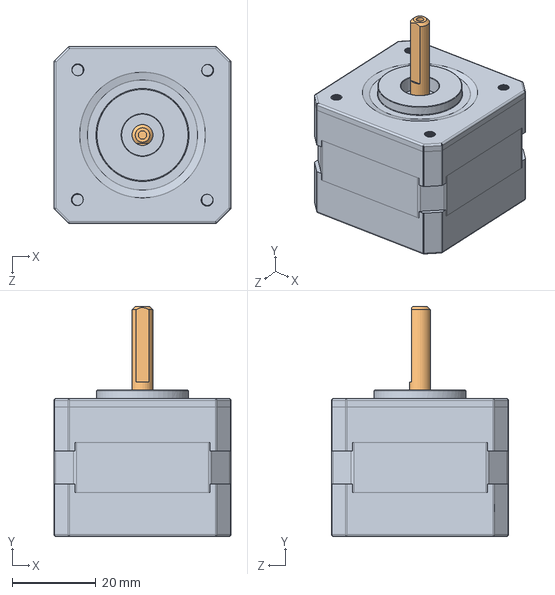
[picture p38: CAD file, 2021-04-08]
Phase 3-Detail Design/2. Mechanical/CAD/Intermediate_Assm/Intermediate_Assem_Rev_B1/324 NEMA-17 Stepper Motor.SLDASM
42.3 x 55.0 x 42.3 mm
Main Stepper Body.step
Shaft.step

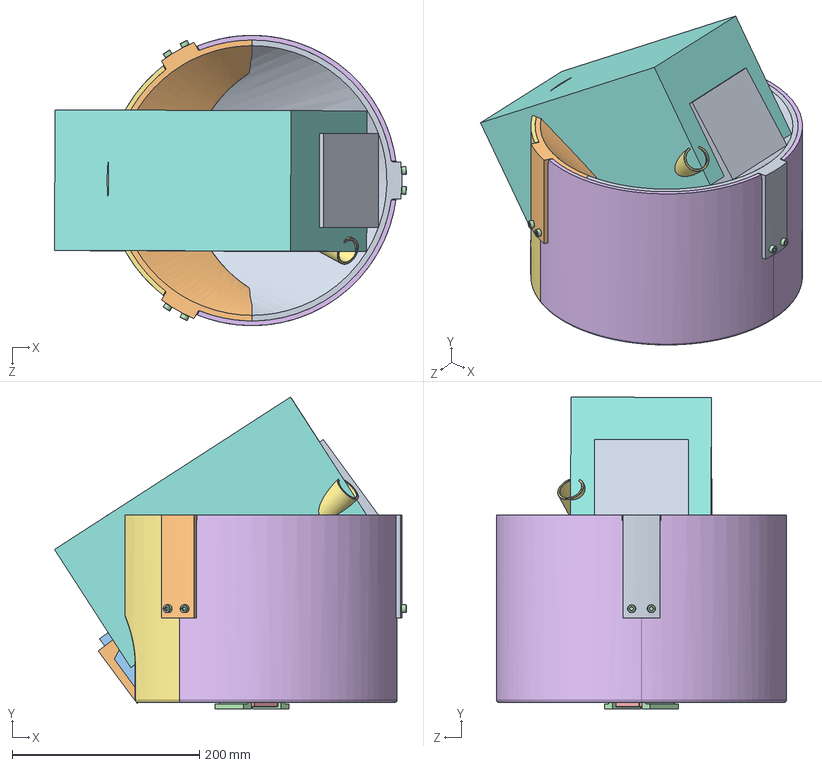
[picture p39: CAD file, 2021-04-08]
Phase 3-Detail Design/2. Mechanical/CAD/Output_Assm/Output_Diverter_Assm_Rev_C/Output_Diverter_Chute_Assm.SLDASM
375.9 x 333.0 x 310.0 mm
Back_Plate
Damping_Lip_Complete
90592A095_STEEL HEX NUT x 10
91290A232_BLACK-OXIDE CLASS 12.9 SOCKET HEAD CAP SCREW x 10
Main Stepper Body.step
Shaft.step
MAX_SIZE_Block
Motor_Mount
90751A111_METRIC FINE-THREAD 18-18 SS SOCKET HEAD SCREW x 4
Outer_Shell_1 x 2
Outer_Shell_2

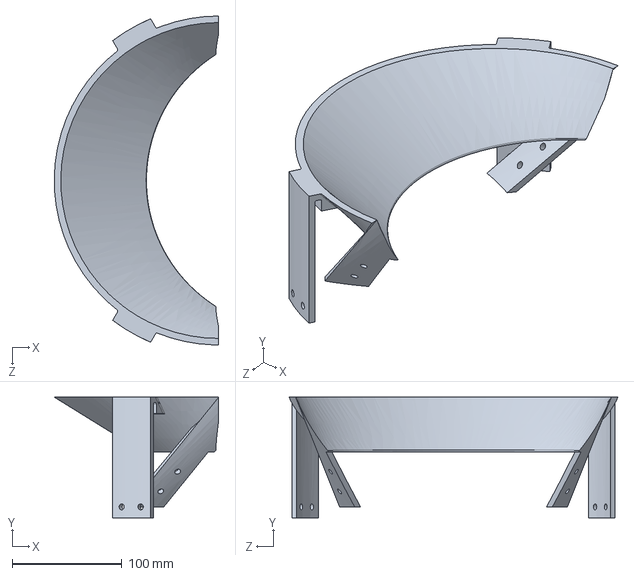
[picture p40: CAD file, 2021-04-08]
Phase 3-Detail Design/2. Mechanical/CAD/Output_Assm/Output_Diverter_Assm_Rev_C/Damping_Lip_Complete.SLDPRT
150.0 x 110.0 x 300.0 mm

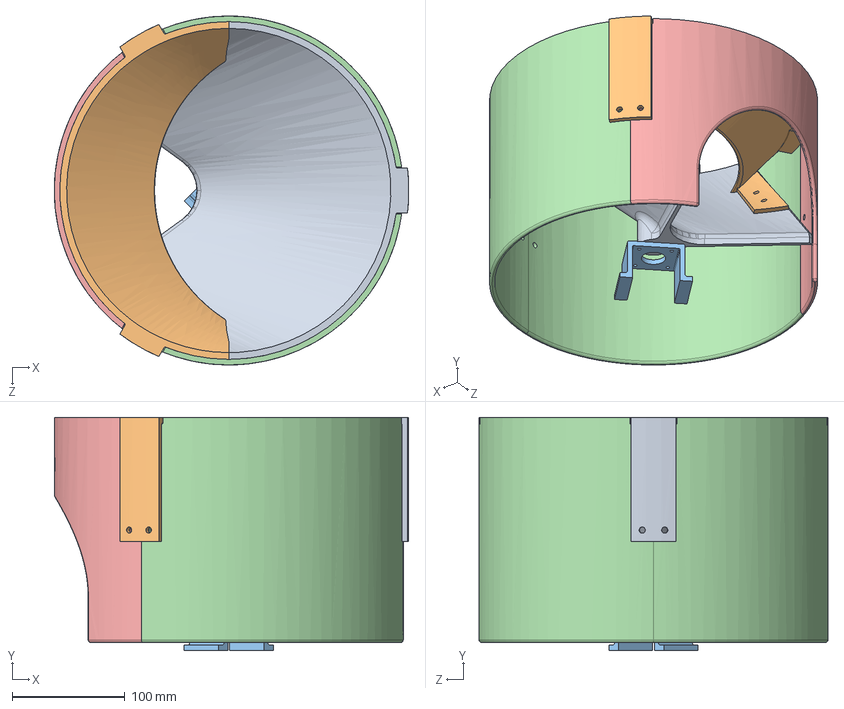
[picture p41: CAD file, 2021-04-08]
Phase 3-Detail Design/2. Mechanical/CAD/Output_Assm/Output_Diverter_Assm_Rev_C1/Output_3D_Printed_Parts_ONLY.SLDASM
314.9 x 207.0 x 310.0 mm
Back_Plate
Damping_Lip_Complete
Motor_Mount
Outer_Shell_1 x 2
Outer_Shell_2

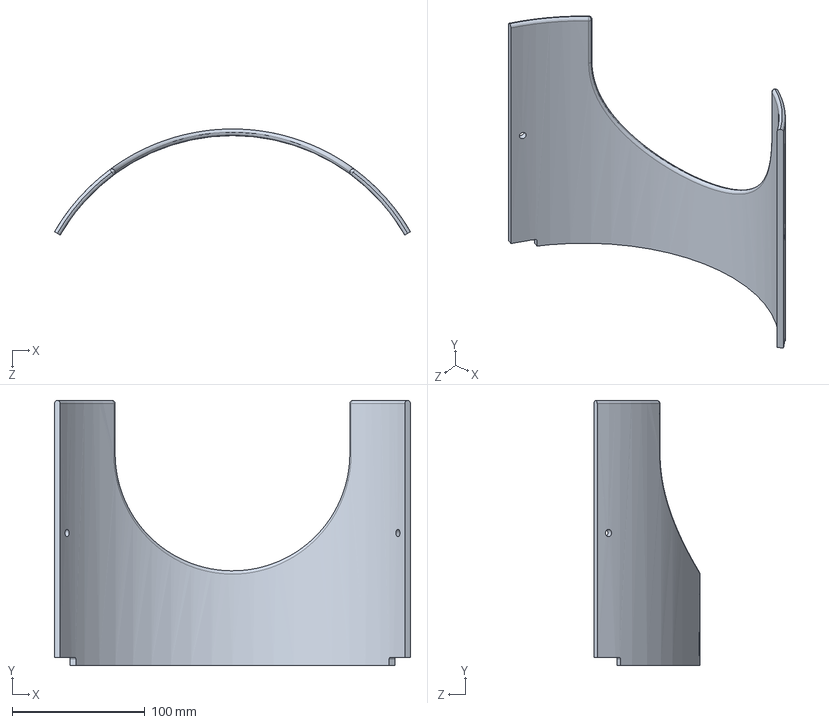
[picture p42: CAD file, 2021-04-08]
Phase 3-Detail Design/2. Mechanical/CAD/CompleteCad/Output/Output_Shell2.SLDPRT
268.5 x 200.0 x 80.0 mm

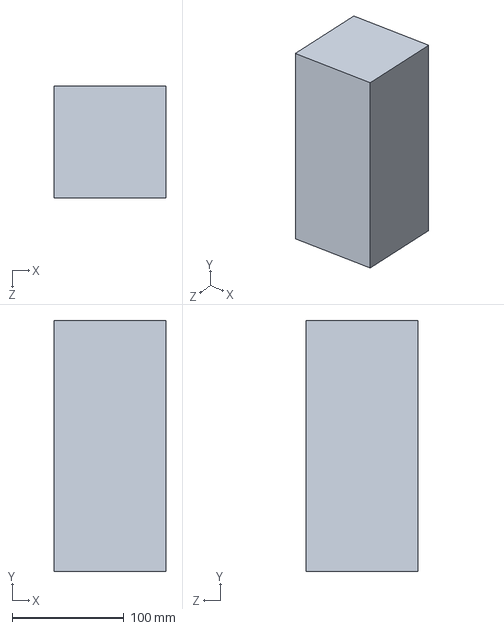
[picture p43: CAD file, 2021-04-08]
Phase 3-Detail Design/2. Mechanical/CAD/CompleteCad/Output/SampleItems/10x10x22.5_Block.SLDPRT
100.0 x 225.0 x 100.0 mm

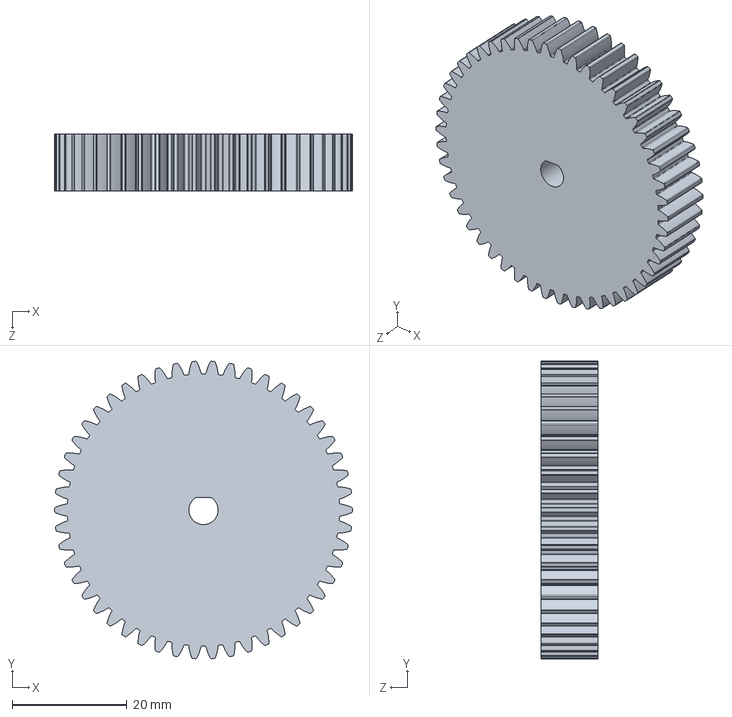
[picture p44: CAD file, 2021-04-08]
Phase 3-Detail Design/2. Mechanical/CAD/CompleteCad/Transmission/Gears&Pulleys/Gear_Mod_1_50_Teeth_5mm_D_bore.SLDPRT
52.0 x 51.9 x 10.0 mm

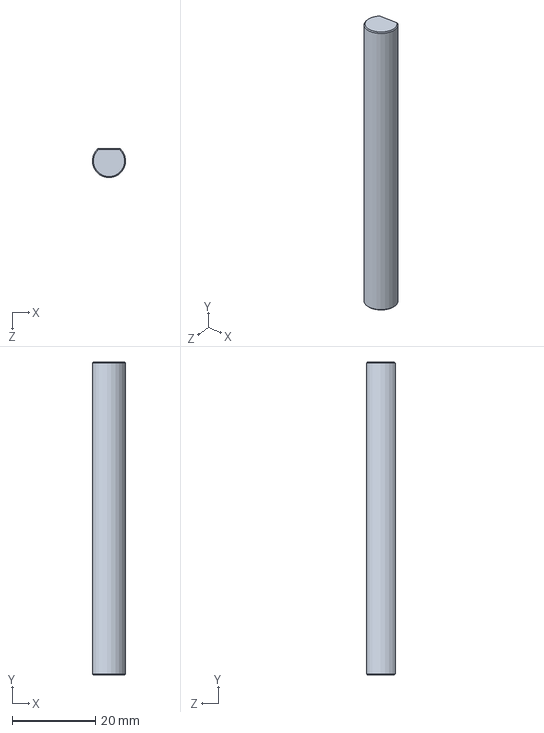
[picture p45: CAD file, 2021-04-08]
Phase 3-Detail Design/2. Mechanical/CAD/CompleteCad/Transmission/Shafts&Bearings/D-Shaft_8mm_OD_short.SLDPRT
7.96 x 75.0 x 6.97 mm

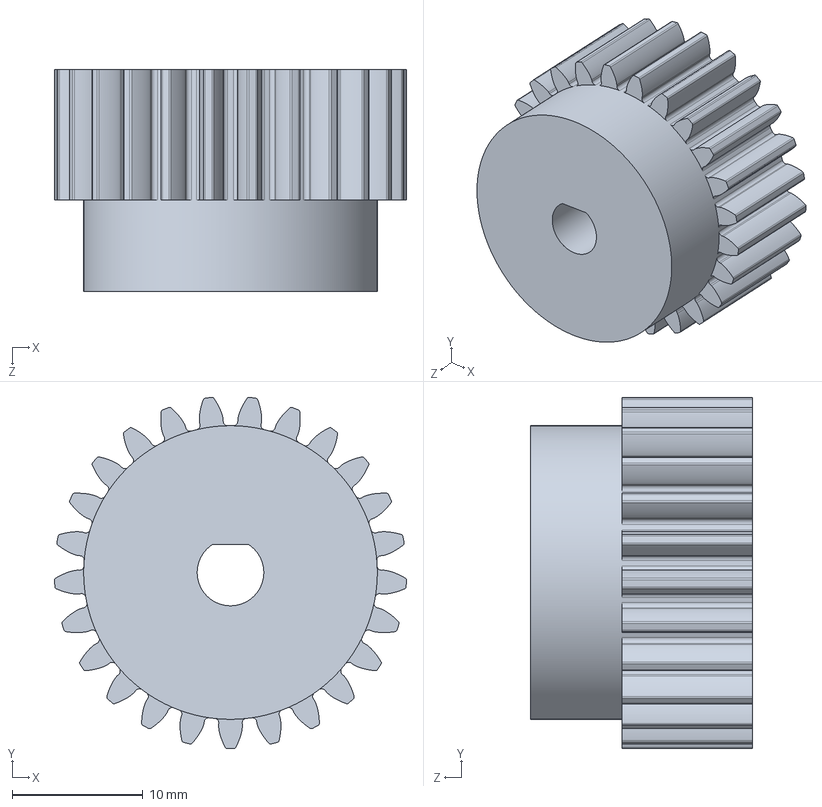
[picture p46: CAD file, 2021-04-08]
Phase 3-Detail Design/2. Mechanical/CAD/Intermediate_Assm/Intermediate_Assem_Rev_B1/Gears & Pulleys/Gear_Mod_1_25_Teeth_5mm_bore.SLDPRT
27.0 x 26.9 x 17.0 mm

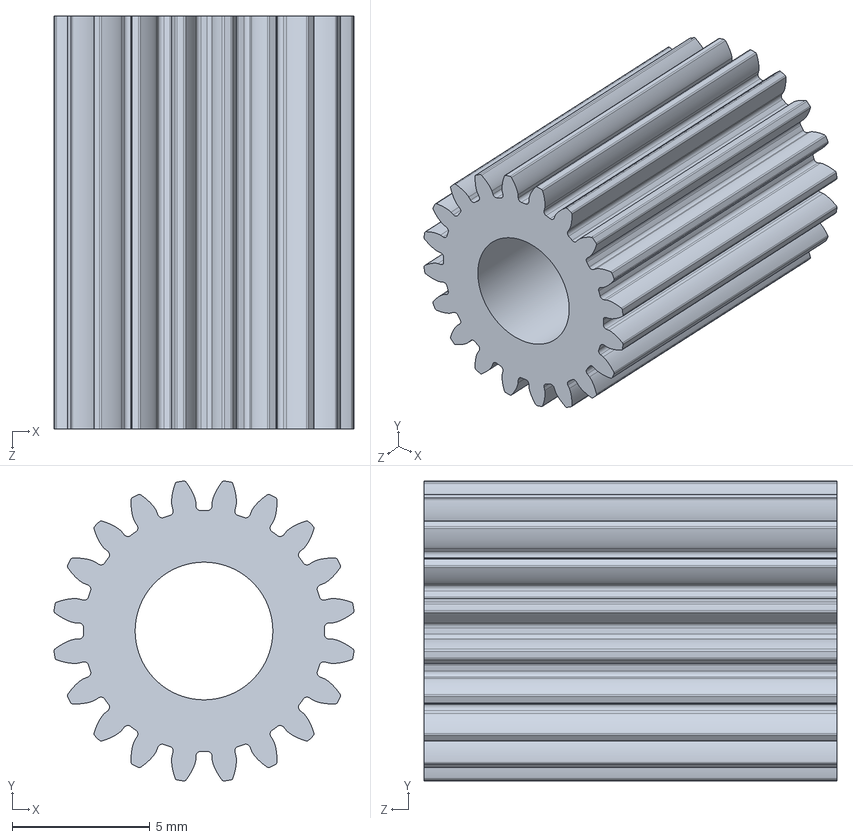
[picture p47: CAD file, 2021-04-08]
Phase 3-Detail Design/2. Mechanical/CAD/Intermediate_Assm/Intermediate_Assem_Rev_B1/Involute Spur Gear Generator/Robust Involute Spur Gear Generator - Better 02.SLDPRT
10.9 x 10.9 x 15.0 mm

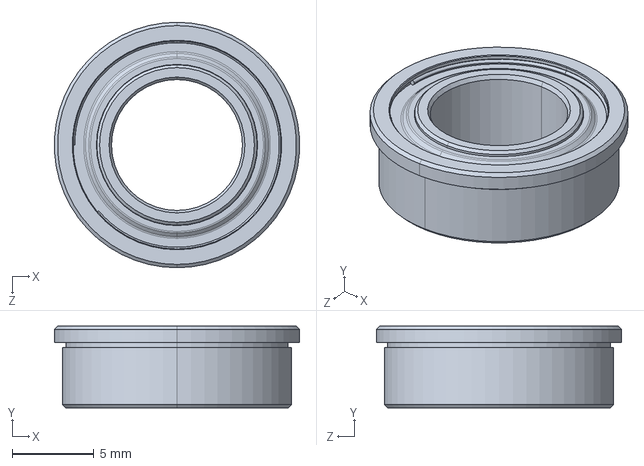
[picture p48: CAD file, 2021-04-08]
Phase 3-Detail Design/2. Mechanical/CAD/Intermediate_Assm/Intermediate_Assem_Rev_B1/Shafts & Bearings/Flanged_Ball_Bearing_8mm_ID.SLDPRT
15.0 x 5.00 x 15.0 mm

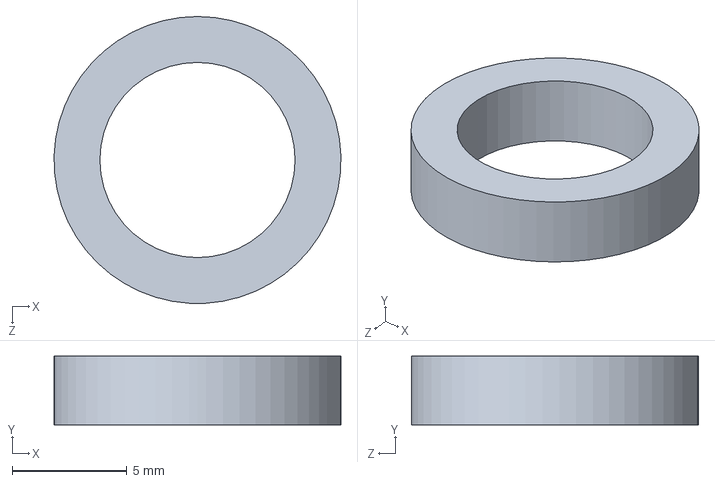
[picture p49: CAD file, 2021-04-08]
Phase 3-Detail Design/2. Mechanical/CAD/Intermediate_Assm/Intermediate_Assem_Rev_B2/3mm Shaft Spacer.SLDPRT
12.5 x 3.00 x 12.5 mm

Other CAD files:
Phase 3-Detail Design/2. Mechanical/CAD/Intermediate_Assm/Intermediate_Assem_Rev_B2/324 NEMA-17 Stepper Motor.SLDASM
Phase 3-Detail Design/2. Mechanical/CAD/Output_Assm/Output_Diverter_Assm_Rev_C1/Output_Diverter_Chute_Assm.SLDASM
Phase 3-Detail Design/2. Mechanical/CAD/CompleteCad/Intermediate/Intermediate_FrontWall.SLDPRT
Phase 3-Detail Design/2. Mechanical/CAD/CompleteCad/Transmission/324 NEMA-17 Stepper Motor.SLDPRT
Phase 3-Detail Design/2. Mechanical/CAD/Intermediate_Assm/Intermediate_Assem_Rev_B2/Gears & Pulleys/Gear_Mod_1_25_Teeth_5mm_D_bore.SLDPRT
Phase 3-Detail Design/2. Mechanical/CAD/Archive/20-3GT09-1AX3_16/20-3GT09-1AX3_16.sldprt
Phase 3-Detail Design/2. Mechanical/CAD/Archive/324 NEMA-17 Stepper Motor.f3d
Phase 3-Detail Design/2. Mechanical/CAD/Archive/GEABB0.5-20-3-B-5_SolidWorks_Native)_=2006_20210228/SOLIDWORKS/GEABB0_5_20_3_B_5.sldasm
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

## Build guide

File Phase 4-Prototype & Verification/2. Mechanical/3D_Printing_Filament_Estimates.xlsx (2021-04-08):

 |  | Per Unit |  |  |  | Total
 | Part (File Name) | Print Time (hour) | Print Time (minute) | Filament length (mm) | Plastic Weight (g) | # Units Needed | Filament length (mm) | Plastic Weight (g) | See Note
1 | Gear_Mod_1_25_Teeth_5mm_D_bore | 0 | 30 | 2203 | 6.62 | 1 | 2203 | 6.62 |  | *Note, assuming it fits in the build volume of the printer in the optimal orientation to have it being printed
2 | Gear_Mod_1_50_Teeth_5mm_D_bore | 0 | 51 | 4132.6 | 14.43 | 2 | 8265.2 | 28.86
3 | Gear_Mod_1_100_Teeth_8mm_D_bore | 2 | 11 | 13087.9 | 39.35 | 2 | 26175.8 | 78.7
4 | Intermediate_4mmSpacer | 0 | 2 | 162.9 | 0.49 | 2 | 325.8 | 0.98
5 | Intermediate_5mmSpacer | 0 | 2 | 152.7 | 0.46 | 4 | 610.8 | 1.84
6 | Intermediate_BackWall | 3 | 35 | 20376.4 | 61.26 | 1 | 20376.4 | 61.26 | *
7 | Intermediate_FrontWall | 3 | 38 | 20338.5 | 61.15 | 1 | 20338.5 | 61.15 | *
8 | Intermediate_LeftGearShield | 12 | 12 | 67454 | 202.81 | 1 | 67454 | 202.81 | *
9 | Intermediate_MidPlate | 2 | 12 | 11677.8 | 35.11 | 1 | 11677.8 | 35.11 | *
10 | Intermediate_MidWall | 3 | 20 | 17966.4 | 54.02 | 1 | 17966.4 | 54.02 | *
11 | Intermediate_MotorMount | 0 | 37 | 3051.4 | 9.17 | 1 | 3051.4 | 9.17 | *
12 | Intermediate_RightGearShield | 4 | 45 | 25218 | 75.82 | 1 | 25218 | 75.82 | *
13 | Intermediate_SideCover | 5 | 34 | 28627.6 | 86.07 | 2 | 57255.2 | 172.14 | *
14 | Intermediate_TrapDoor | 14 | 49 | 82252.8 | 247.3 | 2 | 164505.6 | 494.6 | *
15 | Output_BackPlate | 21 | 9 | 110936.7 | 333.54 | 1 | 110936.7 | 333.54 | *
16 | Output_Lip | 11 | 13 | 56820.7 | 170.84 | 1 | 56820.7 | 170.84 | *
17 | Output_Shell1 | 14 | 46 | 84574 | 254.28 | 2 | 169148 | 508.56 | *
18 | Output_Shell2 | 9 | 17 | 52603.3 | 158.16 | 1 | 52603.3 | 158.16 | *
 |  |  |  |  |  | Total (Intermediate) | 425423.9 | 1283.08
 |  |  |  |  |  | Total (Output) | 389508.7 | 1171.1
 |  |  |  |  |  | Grand Total | 814932.6 | 2454.18

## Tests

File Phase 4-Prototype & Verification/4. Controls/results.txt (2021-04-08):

Glass
64.94%,Paper,
91.18%,Glass,
98.99%,Glass,
49.79%,Metal, Cans-Household,
73.43%,Glass,
96.10%,Glass,
65.62%,Glass,
88.71%,Glass,
68.52%,Glass,
70.75%,Glass,
71.94%,Metal, Cans-Household,
98.99%,Glass,
94.50%,Glass,
61.57%,Glass,
61.94%,Glass,
46.50%,Glass,
93.29%,Glass,
68.97%,Glass,
68.13%,Metal, Cans-Household,
59.63%,Glass,
82.90%,Glass,
35.15%,Paper,
74.82%,Glass,
96.98%,Glass,
39.85%,Glass,
57.01%,Glass,
68.61%,Glass,
94.50%,Glass,
68.20%,Glass,
59.06%,Glass,
52.05%,Glass,
79.53%,Glass,
53.97%,Glass,
71.35%,Glass,
61.88%,Glass,
78.64%,Glass,
55.19%,Glass,

Metal - Aluminum Foil
58.68%,Paper,
43.59%,Paper,
61.99%,Metal, Aluminum Foil,
52.95%,Metal, Aluminum Foil,
75.61%,Metal, Aluminum Foil,
78.86%,Metal, Aluminum Foil,
42.15%,Metal, Cans-Household,
64.18%,Metal, Aluminum Foil,
45.57%,Metal, Aluminum Foil,
48.39%,Paper,
58.70%,Paper,
99.17%,Metal, Aluminum Foil,
97.28%,Metal, Aluminum Foil,
85.52%,Metal, Aluminum Foil,
97.86%,Metal, Aluminum Foil,
95.86%,Metal, Aluminum Foil,
55.54%,Metal, Aluminum Foil,
95.32%,Metal, Aluminum Foil,
91.94%,Metal, Aluminum Foil,
64.79%,Metal, Aluminum Foil,
95.78%,Metal, Aluminum Foil,
87.33%,Metal, Aluminum Foil,
75.27%,Metal, Aluminum Foil,
86.76%,Metal, Aluminum Foil,
97.92%,Metal, Aluminum Foil,
87.43%,Metal, Aluminum Foil,
79.22%,Metal, Aluminum Foil,
92.78%,Metal, Aluminum Foil,
98.75%,Metal, Aluminum Foil,
92.90%,Metal, Aluminum Foil,
97.35%,Metal, Aluminum Foil,
94.67%,Metal, Aluminum Foil,
56.01%,Plastic, All,
99.53%,Metal, Aluminum Foil,
97.97%,Metal, Aluminum Foil,
54.65%,Metal, Aluminum Foil,
85.88%,Metal, Aluminum Foil,
53.77%,Metal, Aluminum Foil,
97.14%,Metal, Aluminum Foil,
91.34%,Metal, Aluminum Foil,
90.39%,Metal, Aluminum Foil,
86.55%,Metal, Aluminum Foil,
92.10%,Metal, Aluminum Foil,
68.90%,Metal, Aluminum Foil,
67.05%,Metal, Aluminum Foil,
74.85%,Metal, Aluminum Foil,
83.72%,Metal, Aluminum Foil,
62.67%,Metal, Aluminum Foil,
75.45%,Metal, Aluminum Foil,
90.88%,Metal, Aluminum Foil,
91.99%,Metal, Aluminum Foil,
77.21%,Metal, Cans-Household,
63.47%,Metal, Cans-Household,
69.45%,Metal, Cans-Household,
80.73%,Metal, Cans-Household,
81.85%,Metal, Cans-Household,
81.93%,Metal, Cans-Household,
86.98%,Metal, Cans-Household,
75.21%,Metal, Cans-Household,
77.38%,Metal, Cans-Household,
80.05%,Metal, Cans-Household,
91.21%,Metal, Cans-Household,
66.50%,Metal, Cans-Household,
54.69%,Metal, Cans-Household,
44.46%,Paper,
60.07%,Metal, Cans-Household,
65.53%,Metal, Cans-Household,
86.53%,Metal, Cans-Household,
44.13%,Metal, Cans-Household,
51.34%,Metal, Cans-Household,
51.72%,Metal, Cans-Household,
78.81%,Metal, Cans-Household,
66.73%,Metal, Cans-Household,
83.73%,Metal, Cans-Household,

Metal Cans
56.13%,Paper,
41.52%,Metal, Aluminum Foil,
85.46%,Metal, Aluminum Foil,
88.12%,Metal, Aluminum Foil,
71.34%,Metal, Aluminum Foil,
50.01%,Metal, Aluminum Foil,
87.45%,Metal, Aluminum Foil,
39.77%,Metal, Aluminum Foil,
79.18%,Metal, Aluminum Foil,
54.29%,Metal, Cans-Household,
65.59%,Metal, Aluminum Foil,
51.53%,Metal, Aluminum Foil,
81.36%,Metal, Cans-Household,
50.87%,Metal, Cans-Household,
79.80%,Metal, Cans-Household,
68.13%,Metal, Cans-Household,
78.34%,Metal, Cans-Household,
80.79%,Metal, Cans-Household,
56.97%,Metal, Aluminum Foil,
75.95%,Metal, Aluminum Foil,
69.46%,Metal, Aluminum Foil,
83.02%,Metal, Aluminum Foil,
51.51%,Metal, Aluminum Foil,
61.44%,Metal, Aluminum Foil,
88.31%,Metal, Aluminum Foil,
94.87%,Metal, Cans-Household,
97.77%,Metal, Cans-Household,
96.95%,Metal, Cans-Household,
98.01%,Metal, Cans-Household,
94.27%,Metal, Cans-Household,
93.91%,Metal, Cans-Household,
98.38%,Metal, Cans-Household,
99.06%,Metal, Cans-Household,
96.18%,Metal, Cans-Household,
86.50%,Metal, Cans-Household,
96.69%,Metal, Cans-Household,
97.62%,Metal, Cans-Household,
99.68%,Metal, Cans-Household,
99.56%,Metal, Cans-Household,
98.35%,Metal, Cans-Household,
99.91%,Metal, Cans-Household,
99.43%,Metal, Cans-Household,
99.65%,Metal, Cans-Household,
99.99%,Metal, Cans-Household,
98.45%,Metal, Cans-Household,
99.95%,Metal, Cans-Household,
96.64%,Metal, Cans-Household,
82.08%,Metal, Cans-Household,
99.95%,Metal, Cans-Household,
94.81%,Metal, Cans-Household,
94.81%,Metal, Cans-Household,
72.13%,Metal, Cans-Household,
72.13%,Metal, Cans-Household,
58.46%,Plastic, Black,
54.59%,Glass,
51.09%,Glass,
99.97%,Metal, Cans-Household,
74.70%,Metal, Cans-Household,
67.10%,Metal, Cans-Household,
99.85%,Metal, Cans-Household,
80.56%,Metal, Cans-Household,
68.82%,Metal, Cans-Household,
68.82%,Metal, Cans-Household,
65.64%,Metal, Cans-Household,
65.64%,Metal, Cans-Household,
53.27%,Plastic, Black,
56.56%,Metal, Cans-Household,
99.98%,Metal, Cans-Household,
64.83%,Metal, Cans-Household,
96.11%,Metal, Cans-Household,
62.79%,Metal, Cans-Household,
62.29%,Metal, Cans-Household,
100.00%,Metal, Cans-Household,
90.36%,Metal, Cans-Household,
61.60%,Metal, Cans-Household,
85.36%,Metal, Cans-Household,
87.46%,Glass,
56.45%,Glass,
52.41%,Paper,
49.35%,Glass,
59.05%,Glass,
69.93%,Metal, Cans-Household,
87.64%,Metal, Cans-Household,
45.94%,Metal, Cans-Household,
55.69%,Glass,

NA_Background
31.75%,NA, Background,
39.08%,NA, Background,
47.58%,NA, Background,
36.14%,NA, Background,
36.17%,NA, Background,
35.83%,NA, Background,
30.78%,NA, Background,
33.85%,NA, Background,
56.40%,NA, Background,
77.65%,NA, Background,
46.24%,NA, Background,
85.61%,NA, Background,
90.09%,NA, Background,
89.17%,NA, Background,
85.85%,NA, Background,
86.29%,NA, Background,
87.93%,NA, Background,
33.02%,NA, Background,
34.73%,NA, Background,
62.32%,Metal, Cans-Household,
44.49%,Metal, Cans-Household,
74.97%,Metal, Cans-Household,
47.23%,Metal, Aluminum Foil,
64.89%,Plastic, All,
59.34%,Plastic, All,
36.55%,NA, Background,
36.64%,NA, Background,
46.50%,Metal, Aluminum Foil,
65.36%,Plastic, All,
45.62%,NA, Background,
57.42%,Plastic, All,
45.69%,Plastic, All,
47.83%,Plastic, All,
46.37%,Plastic, All,

Paper
97.88%,Paper,
95.86%,Paper,
96.31%,Paper,
82.14%,Paper,
88.21%,Paper,
97.29%,Paper,
96.61%,Paper,
96.60%,Paper,
41.70%,Metal, Aluminum Foil,
79.20%,Paper,
89.24%,Paper,
78.78%,Paper,
99.20%,Paper,
98.74%,Paper,
98.86%,Paper,
97.90%,Paper,
98.62%,Paper,
71.82%,Paper,
87.22%,Paper,
99.34%,Paper,
99.08%,Paper,
99.07%,Paper,
98.43%,Paper,
97.22%,Paper,
92.41%,Paper,
75.62%,Paper,
51.83%,Paper,
44.77%,Metal, Cans-Household,
48.43%,Paper,
56.88%,Metal, Cans-Household,
75.75%,Paper,
81.48%,Paper,
73.63%,Paper,
91.69%,Paper,
99.37%,Paper,
99.86%,Paper,
96.02%,Paper,
52.79%,Paper,
99.48%,Paper,
81.47%,Paper,
95.99%,Paper,
94.47%,Paper,
94.21%,Paper,
95.55%,Paper,
99.50%,Paper,
77.81%,Paper,
72.91%,Metal, Cans-Household,
35.76%,Paper,
80.91%,Paper,
99.51%,Paper,
92.79%,Paper,
96.49%,Paper,
99.23%,Paper,
95.94%,Paper,
98.56%,Paper,
99.20%,Paper,
51.21%,Paper,
99.34%,Paper,
85.40%,Paper,
90.09%,Paper,
84.01%,Paper,
96.70%,Paper,
88.65%,Paper,
69.02%,Paper,
87.84%,Paper,
56.93%,Paper,
89.19%,Paper,
86.02%,Paper,
59.19%,Glass,
48.83%,Metal, Cans-Household,
78.10%,Paper,
70.14%,Paper,
66.33%,Paper,
94.67%,Paper,
65.05%,Metal, Cans-Household,
65.46%,Paper,
70.21%,Paper,
62.83%,Metal, Cans-Household,
52.76%,Paper,
97.92%,Paper,
90.15%,Paper,
68.22%,Paper,
81.44%,Paper,
52.71%,Metal, Cans-Household,
69.96%,Paper,
82.39%,Paper,
54.64%,Paper,
81.79%,Metal, Cans-Household,
93.07%,Paper,
98.72%,Paper,
73.66%,Paper,
93.02%,Paper,
92.21%,Paper,
67.40%,Paper,
88.14%,Paper,
48.44%,Glass,
92.41%,Paper,

Plastic-all

99.09%,Plastic, Black,
95.00%,Plastic, Black,
94.97%,Plastic, Black,
97.37%,Plastic, Black,
98.15%,Plastic, Black,
91.01%,Plastic, Black,
95.56%,Plastic, Black,
98.00%,Plastic, Black,
78.22%,Plastic, Black,
74.87%,Plastic, Black,
70.36%,Plastic, Black,
44.54%,Plastic, Black,
80.10%,Plastic, Black,
83.75%,Plastic, Black,
70.25%,Plastic, Black,
78.84%,Plastic, Black,
68.50%,Plastic, Black,
95.14%,Plastic, Black,
95.09%,Plastic, Black,
68.87%,Plastic, Black,
61.79%,Plastic, Black,
93.55%,Plastic, Black,

Plastic - Black

94.69%,Plastic, All,
67.19%,Plastic, All,
52.82%,Plastic, All,
85.33%,Plastic, All,
94.75%,Plastic, All,
55.64%,Plastic, All,
70.81%,Plastic, All,
77.38%,Plastic, All,
58.27%,Plastic, All,
64.28%,Plastic, All,
69.97%,Plastic, All,
80.25%,Plastic, All,
52.90%,Metal, Aluminum Foil,
55.81%,Metal, Aluminum Foil,
69.39%,Plastic, All,
80.51%,Plastic, All,
79.37%,Plastic, All,
74.59%,Plastic, All,
83.11%,Plastic, All,
97.11%,Plastic, All,
98.62%,Plastic, All,
78.78%,Plastic, All,
77.01%,Plastic, All,
52.95%,Metal, Aluminum Foil,
75.97%,Metal, Aluminum Foil,
58.52%,Plastic, All,
59.87%,Plastic, All,
86.19%,Plastic, All,
51.44%,Plastic, All,
62.82%,Metal, Aluminum Foil,
69.62%,Plastic, All,
56.46%,Metal, Aluminum Foil,
92.29%,Plastic, All,
61.08%,Metal, Aluminum Foil,
59.55%,Plastic, All,
60.71%,Plastic, All,
85.52%,Plastic, All,
67.12%,Metal, Aluminum Foil,
63.05%,Metal, Aluminum Foil,
67.90%,Metal, Aluminum Foil,
66.12%,Metal, Aluminum Foil,
54.81%,Metal, Aluminum Foil,
50.19%,Metal, Aluminum Foil,
42.44%,NA, Background,
43.87%,Metal, Aluminum Foil,
59.65%,Metal, Aluminum Foil,
60.67%,Metal, Aluminum Foil,
47.39%,Metal, Aluminum Foil,
52.46%,Metal, Aluminum Foil,
27.34%,Metal, Aluminum Foil,
31.51%,Metal, Aluminum Foil,
51.96%,Metal, Aluminum Foil,
51.41%,Metal, Aluminum Foil,
64.97%,Plastic, All,
79.48%,Plastic, All,
73.72%,Plastic, All,
47.19%,Plastic, All,
55.26%,Metal, Aluminum Foil,
47.32%,Metal, Aluminum Foil,
32.76%,Metal, Aluminum Foil,
37.43%,Metal, Aluminum Foil,
43.54%,Plastic, All,
48.12%,Plastic, All,
53.13%,Plastic, All,
45.21%,Plastic, All,
34.73%,Metal, Aluminum Foil,
42.77%,Metal, Aluminum Foil,
48.77%,Metal, Aluminum Foil,
47.69%,Metal, Aluminum Foil,
37.40%,NA, Background,

Stryofoam

95.38%,Styrofoam,
79.34%,Paper,
59.25%,Paper,
91.94%,Styrofoam,

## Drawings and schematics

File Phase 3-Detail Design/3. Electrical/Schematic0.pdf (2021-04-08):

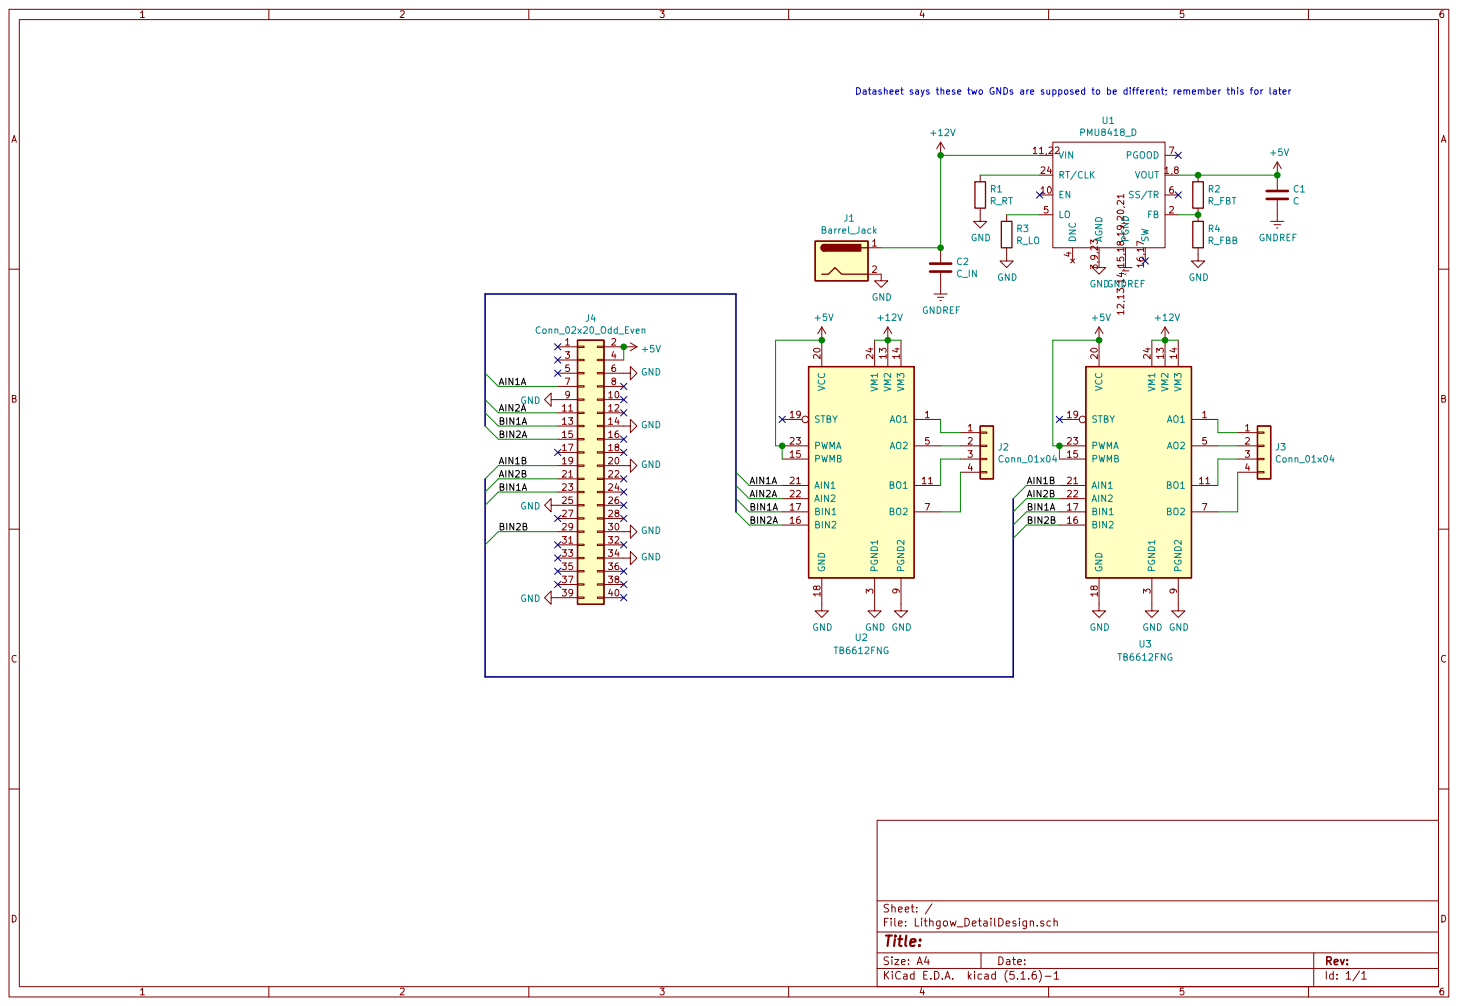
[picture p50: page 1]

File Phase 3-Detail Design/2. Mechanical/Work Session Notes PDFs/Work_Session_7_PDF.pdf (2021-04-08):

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

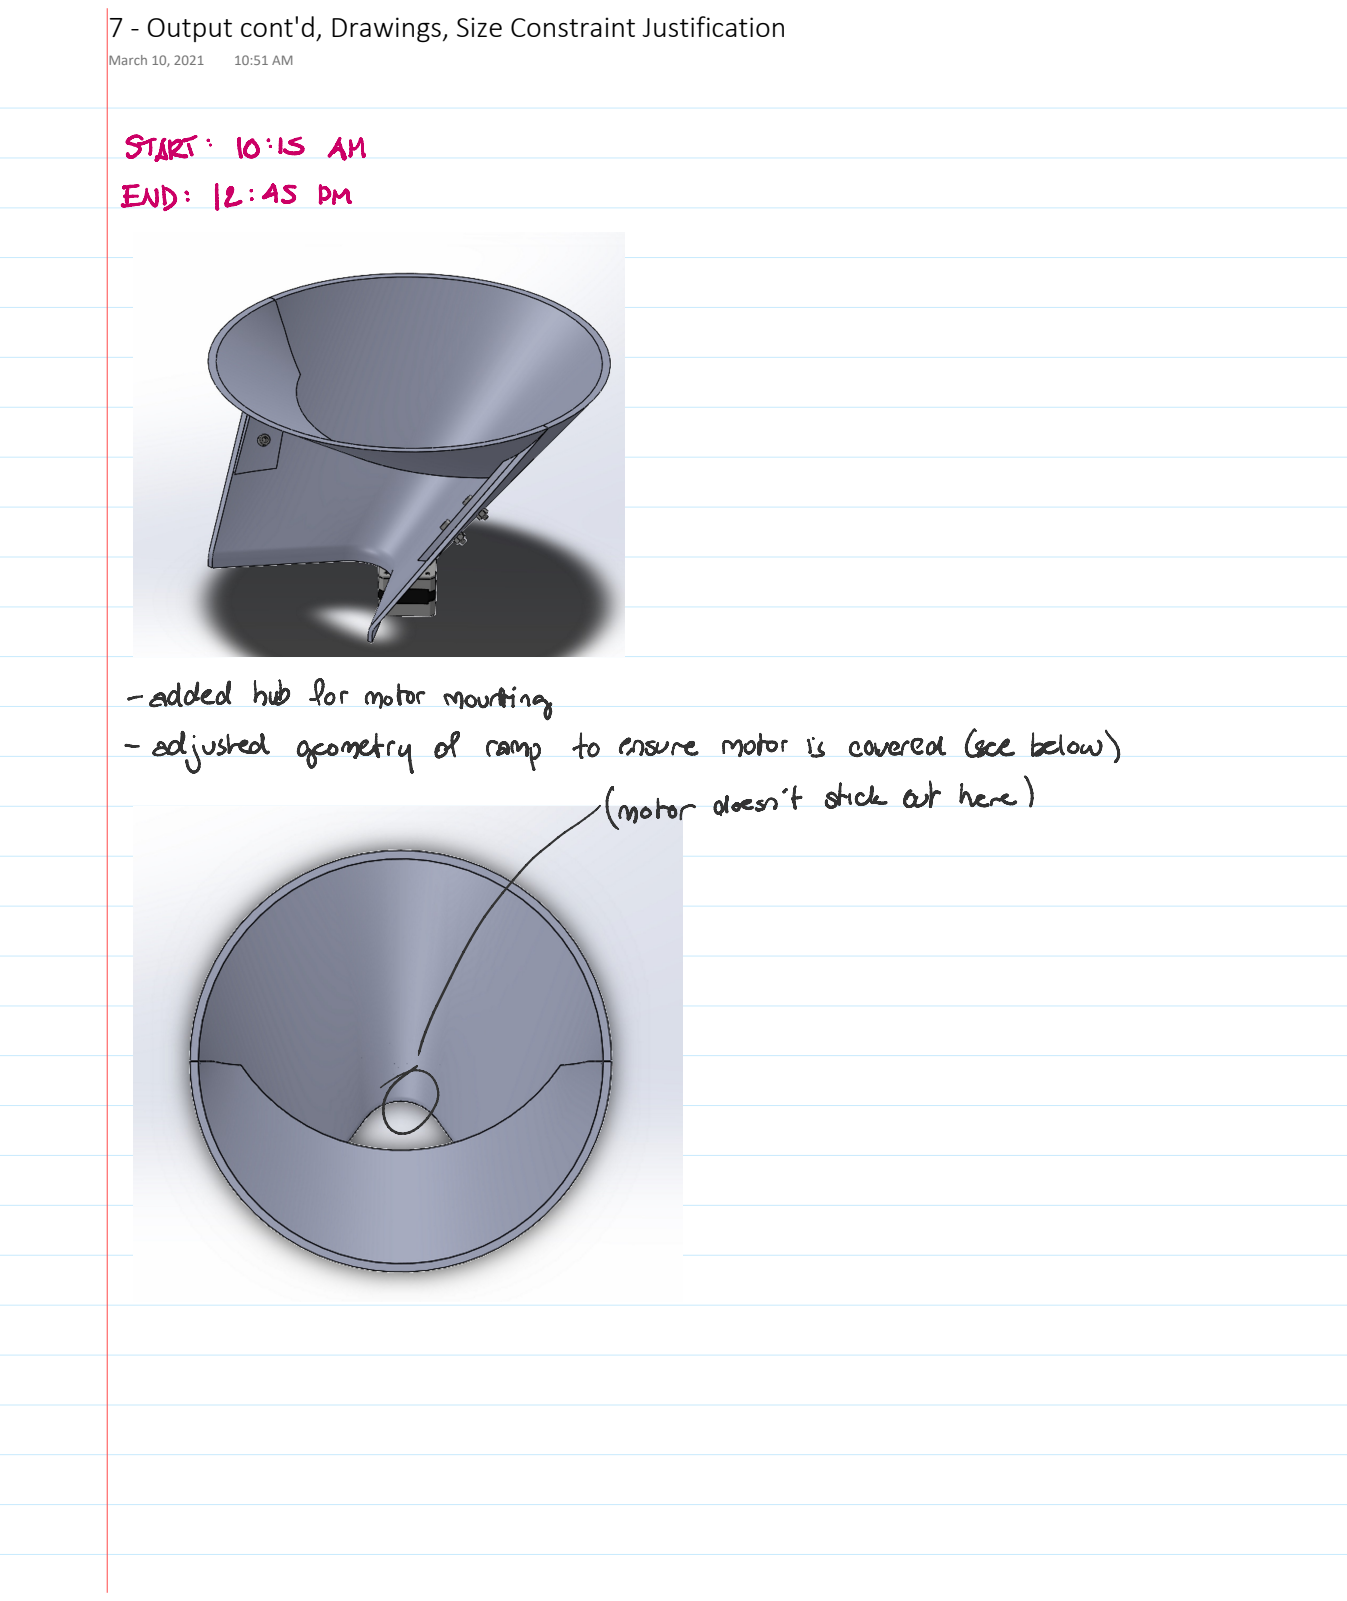
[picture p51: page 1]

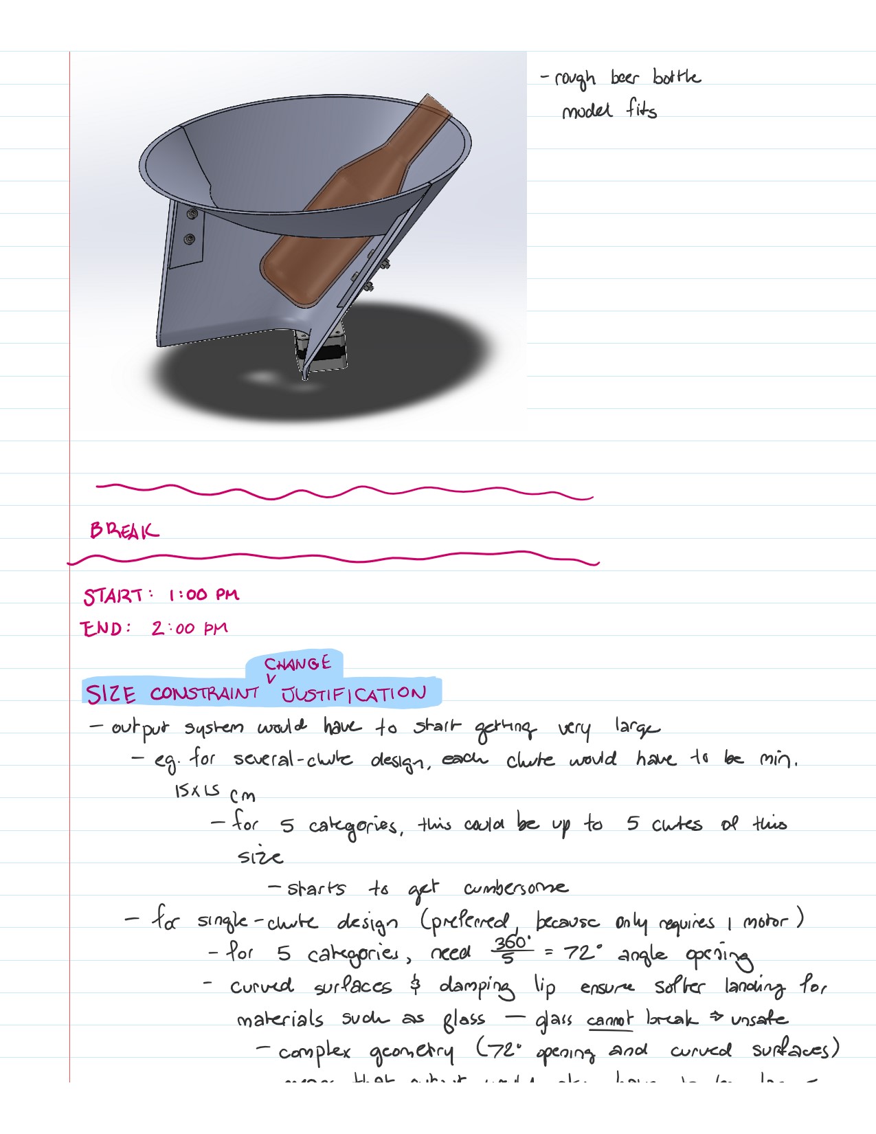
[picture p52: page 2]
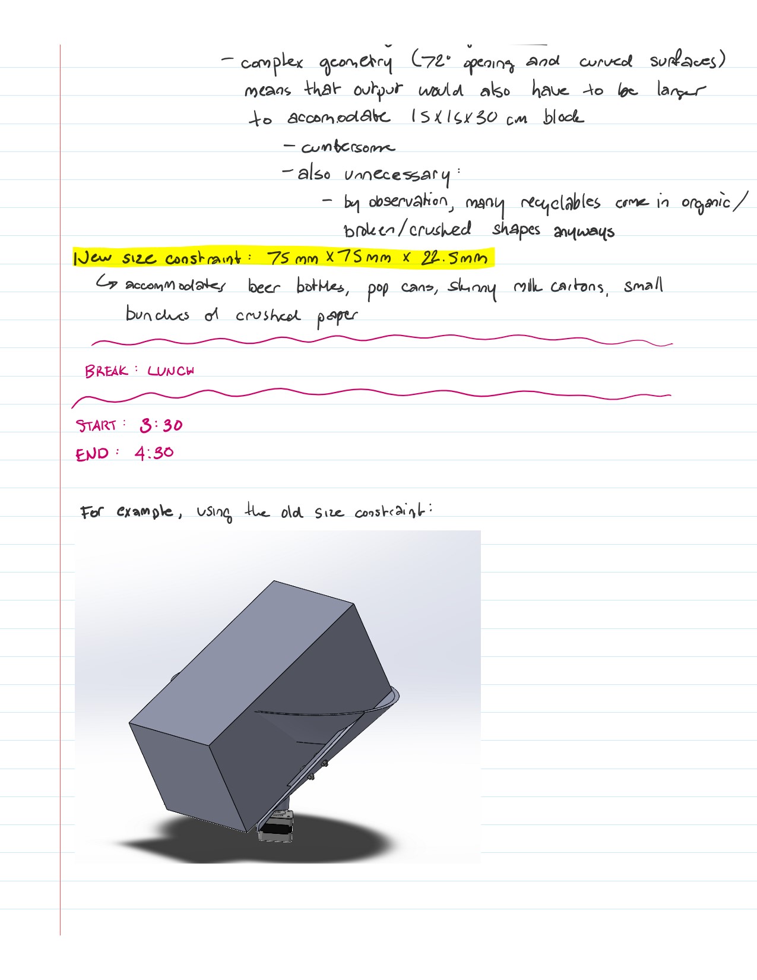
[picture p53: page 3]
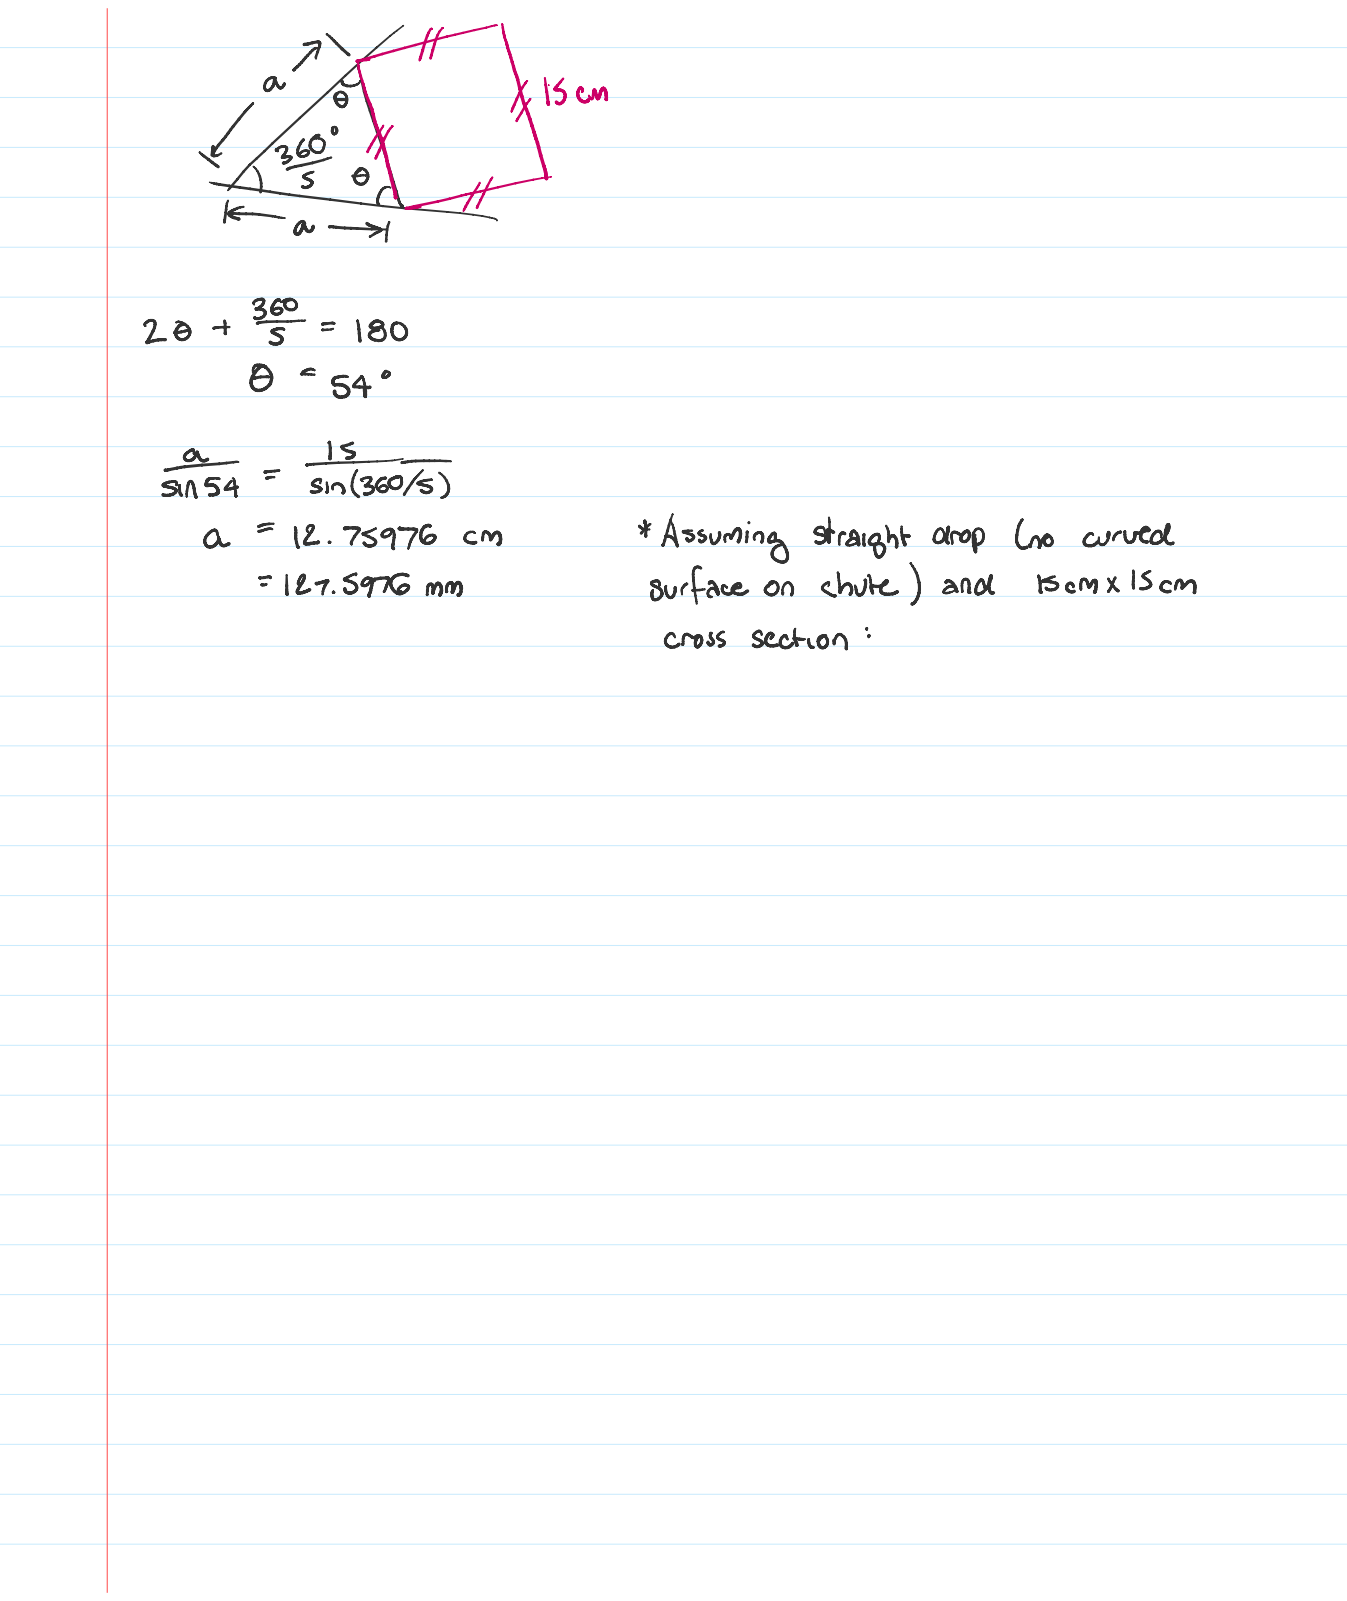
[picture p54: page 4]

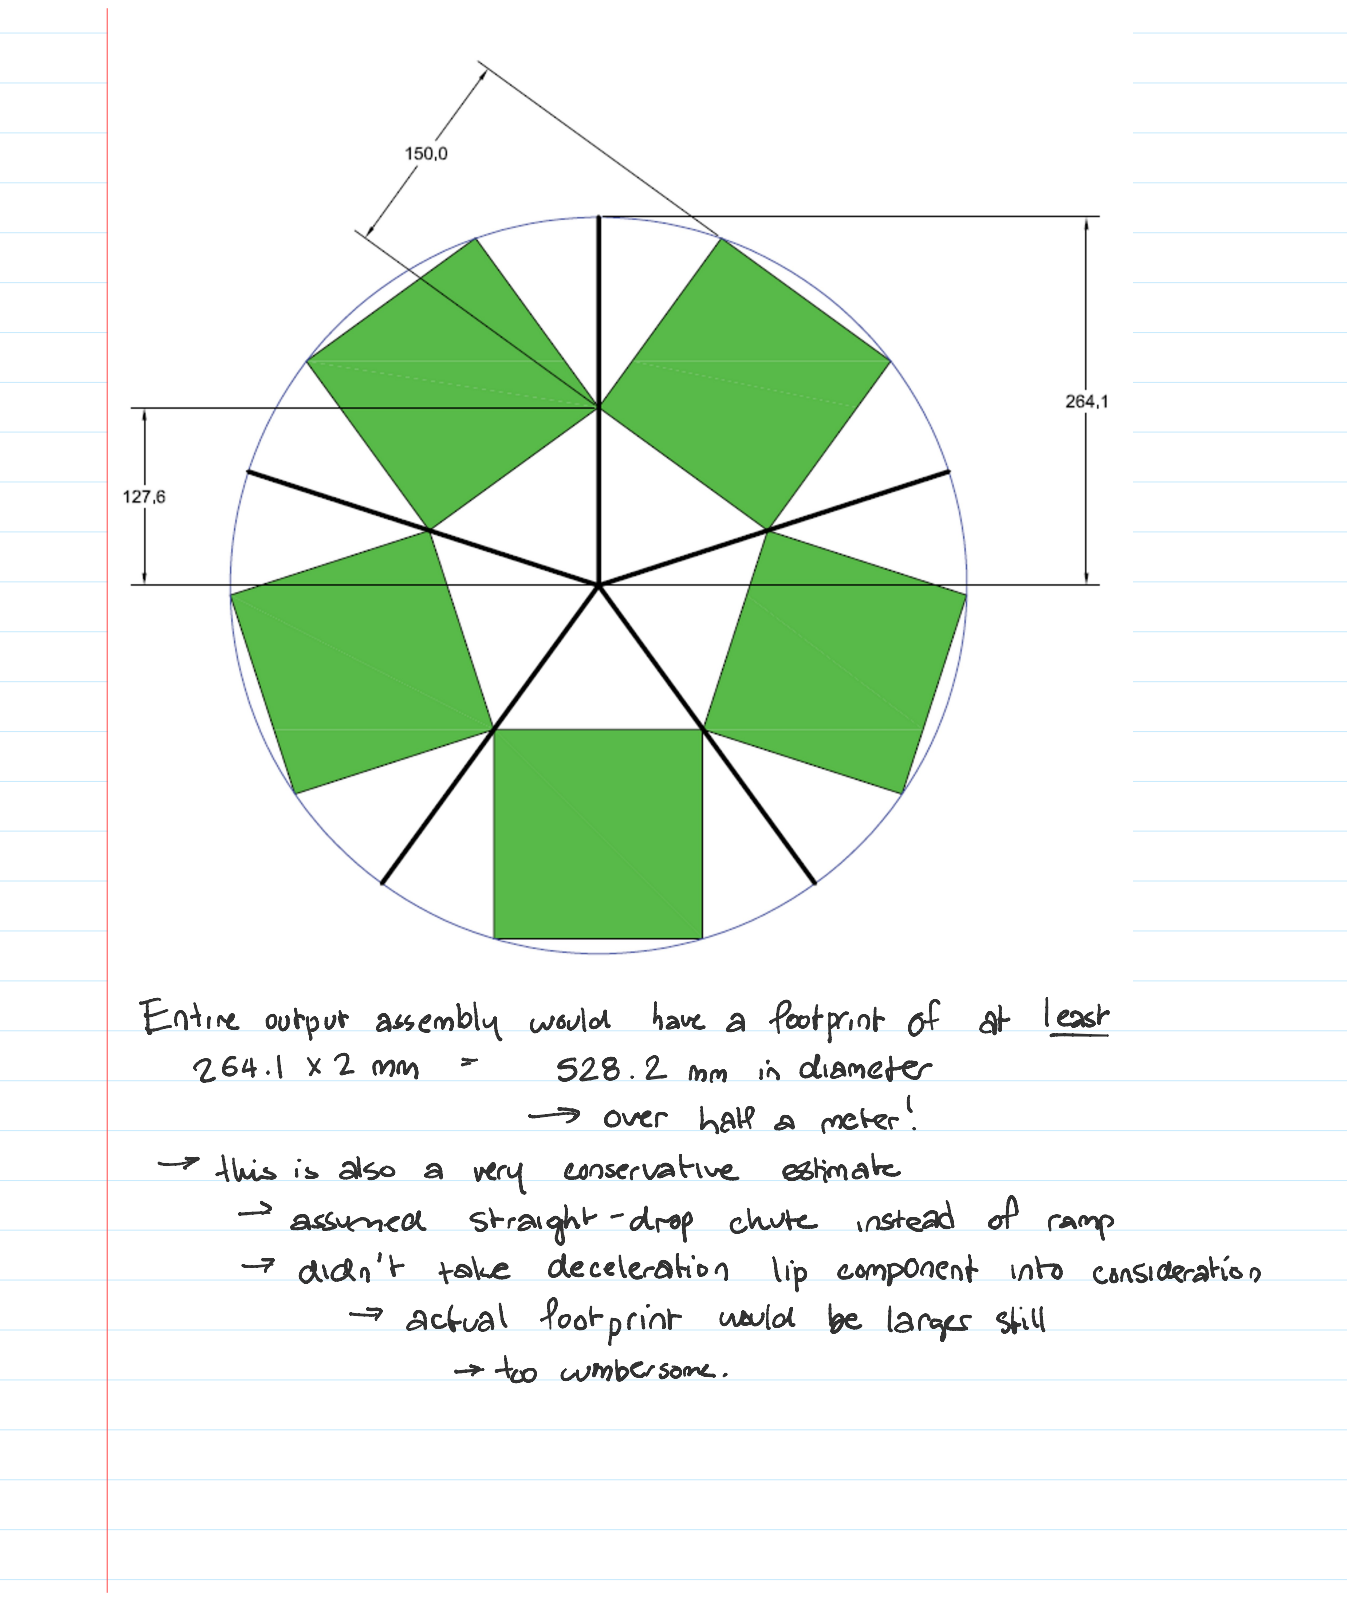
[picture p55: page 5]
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

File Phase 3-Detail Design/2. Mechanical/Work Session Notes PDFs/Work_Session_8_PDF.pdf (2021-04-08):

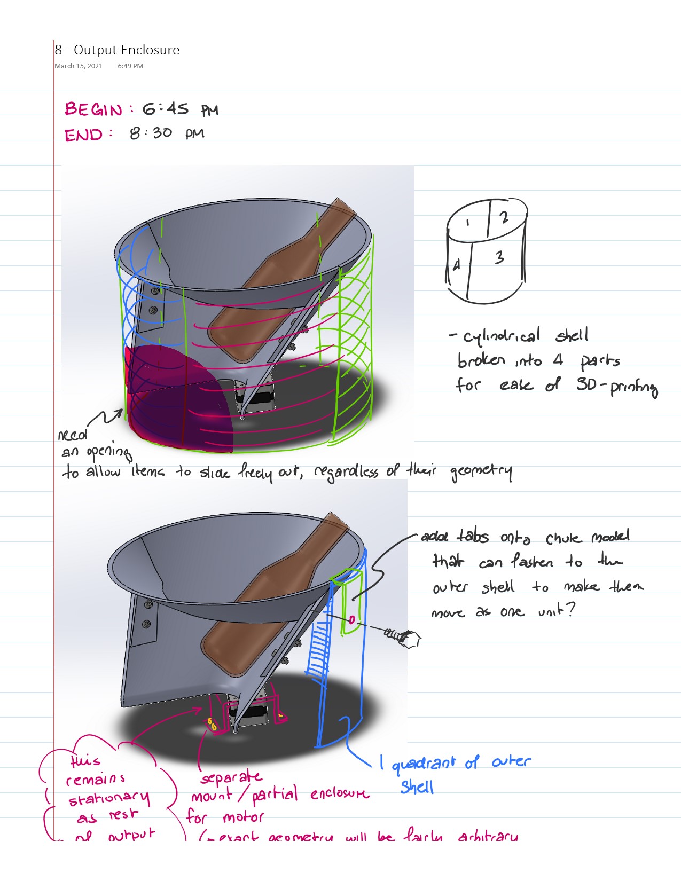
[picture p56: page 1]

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

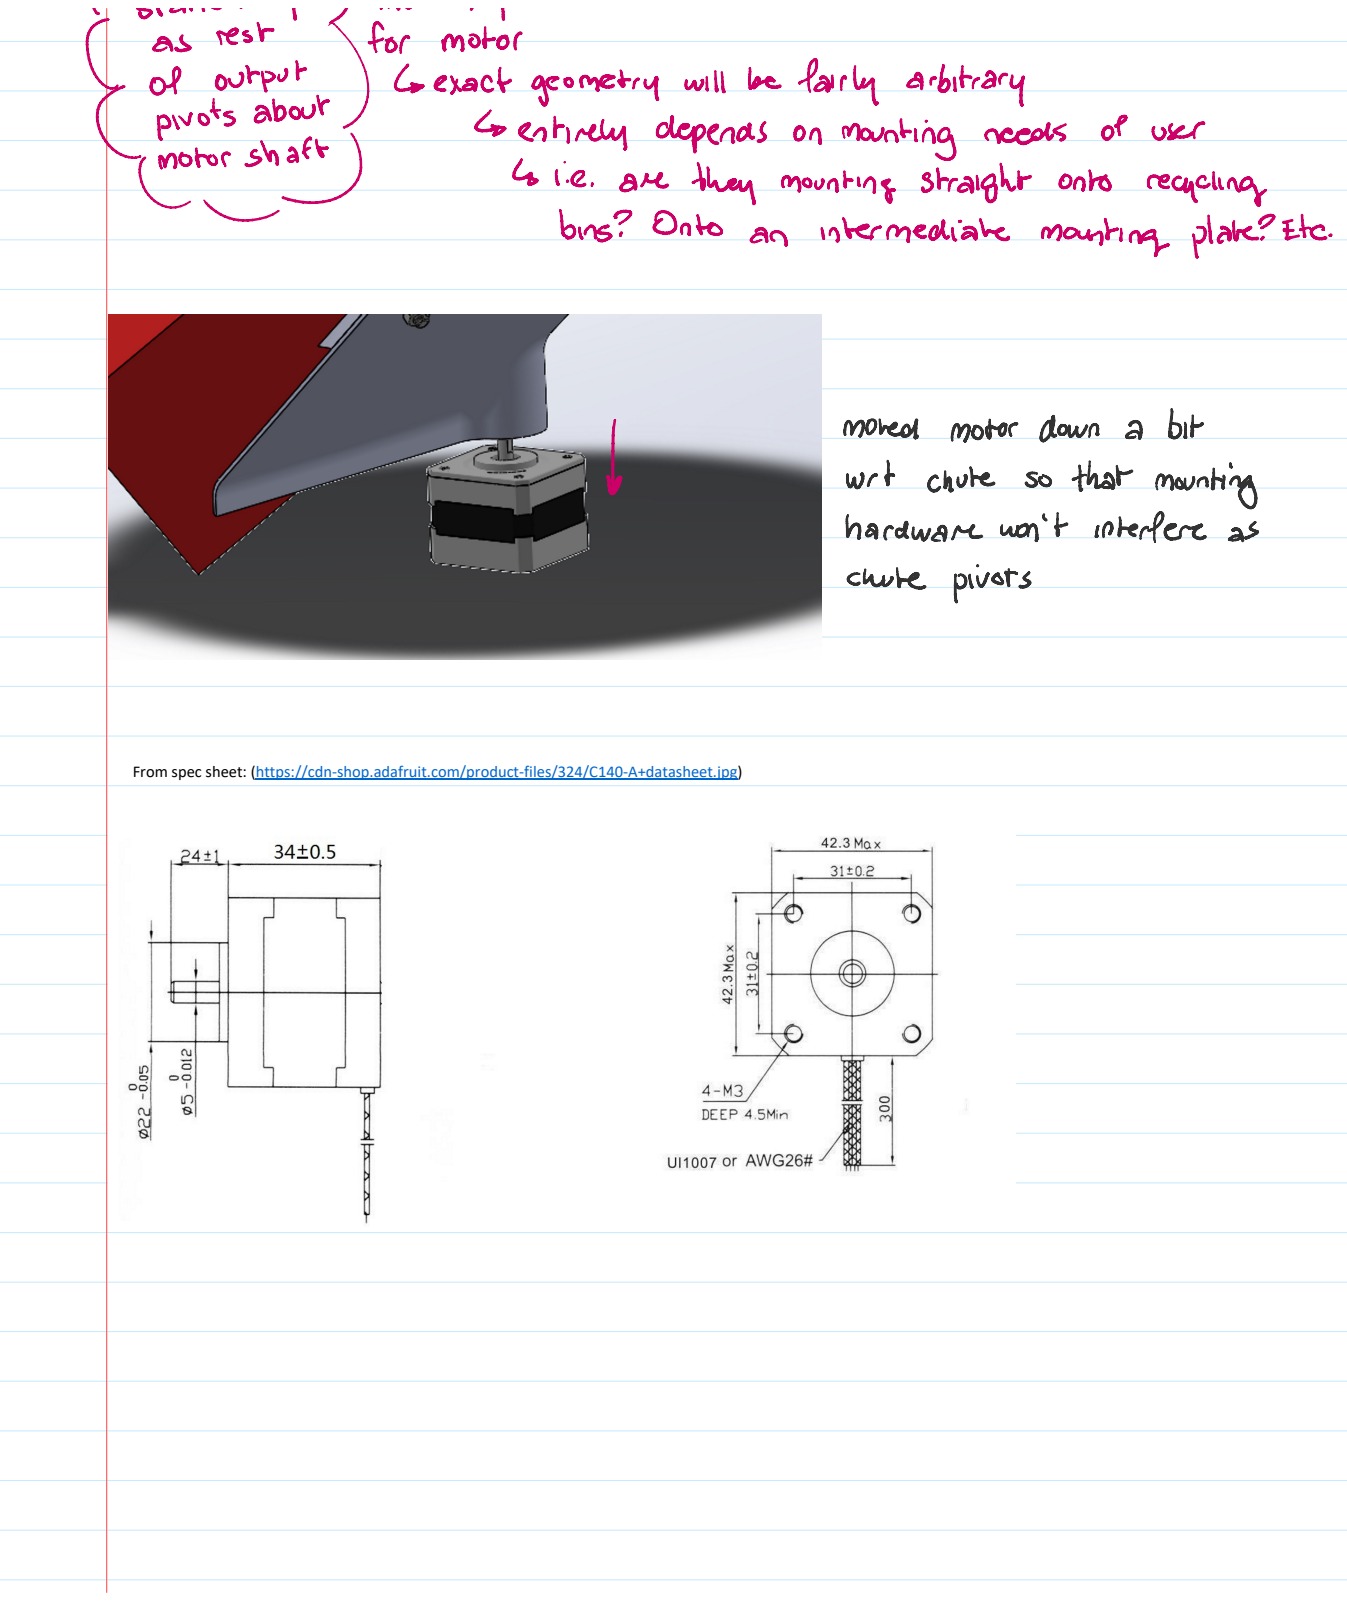
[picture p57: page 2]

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

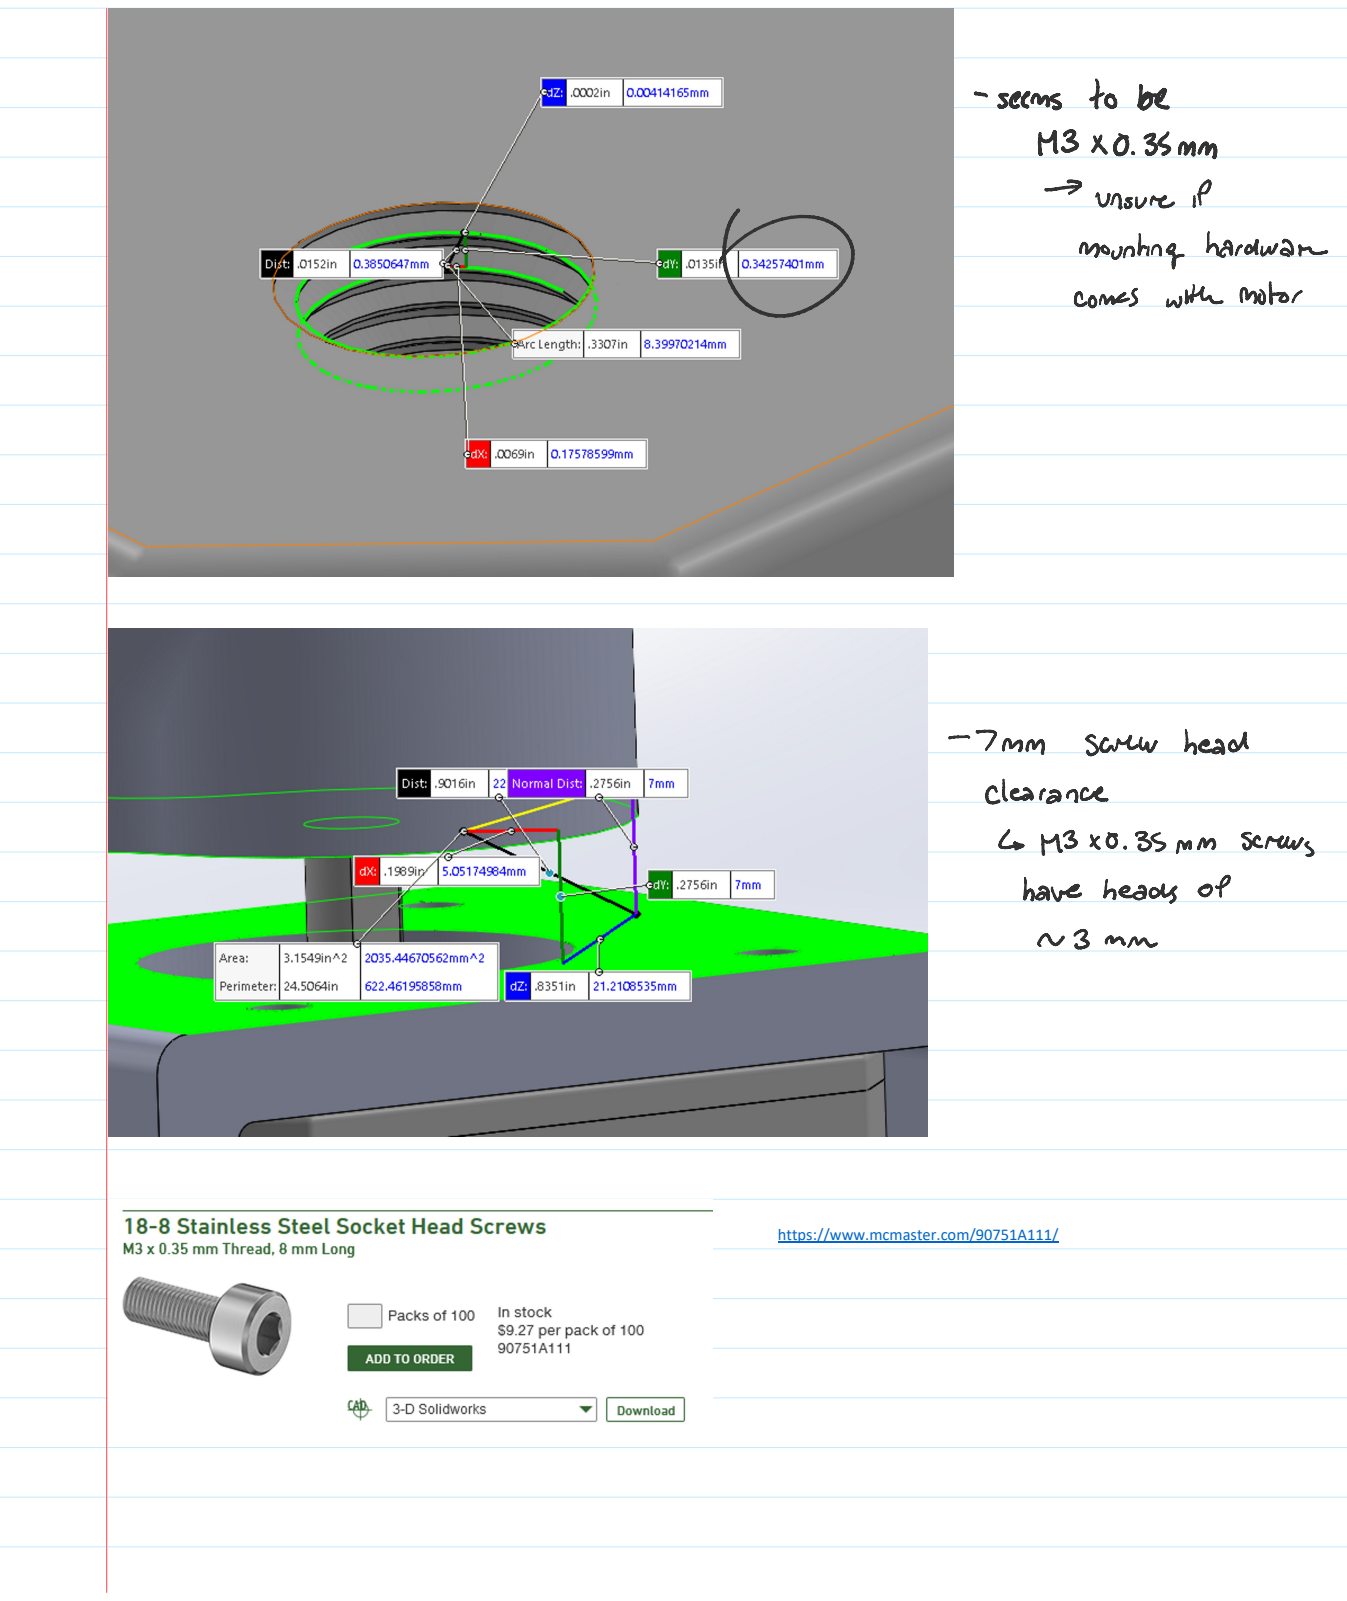
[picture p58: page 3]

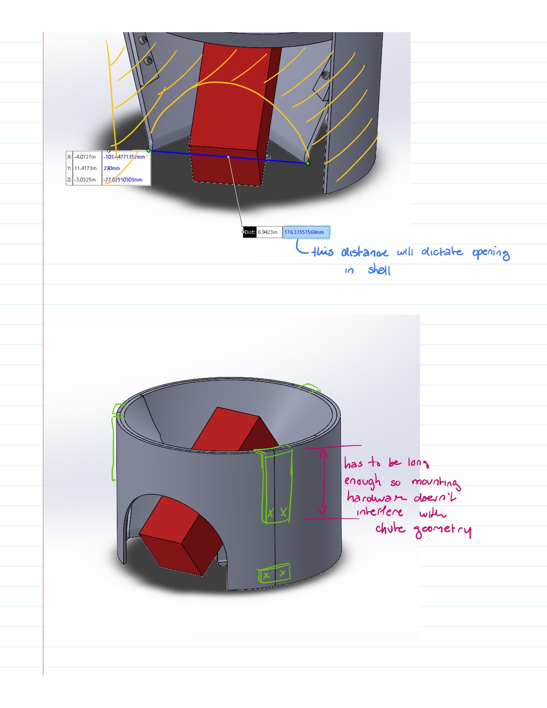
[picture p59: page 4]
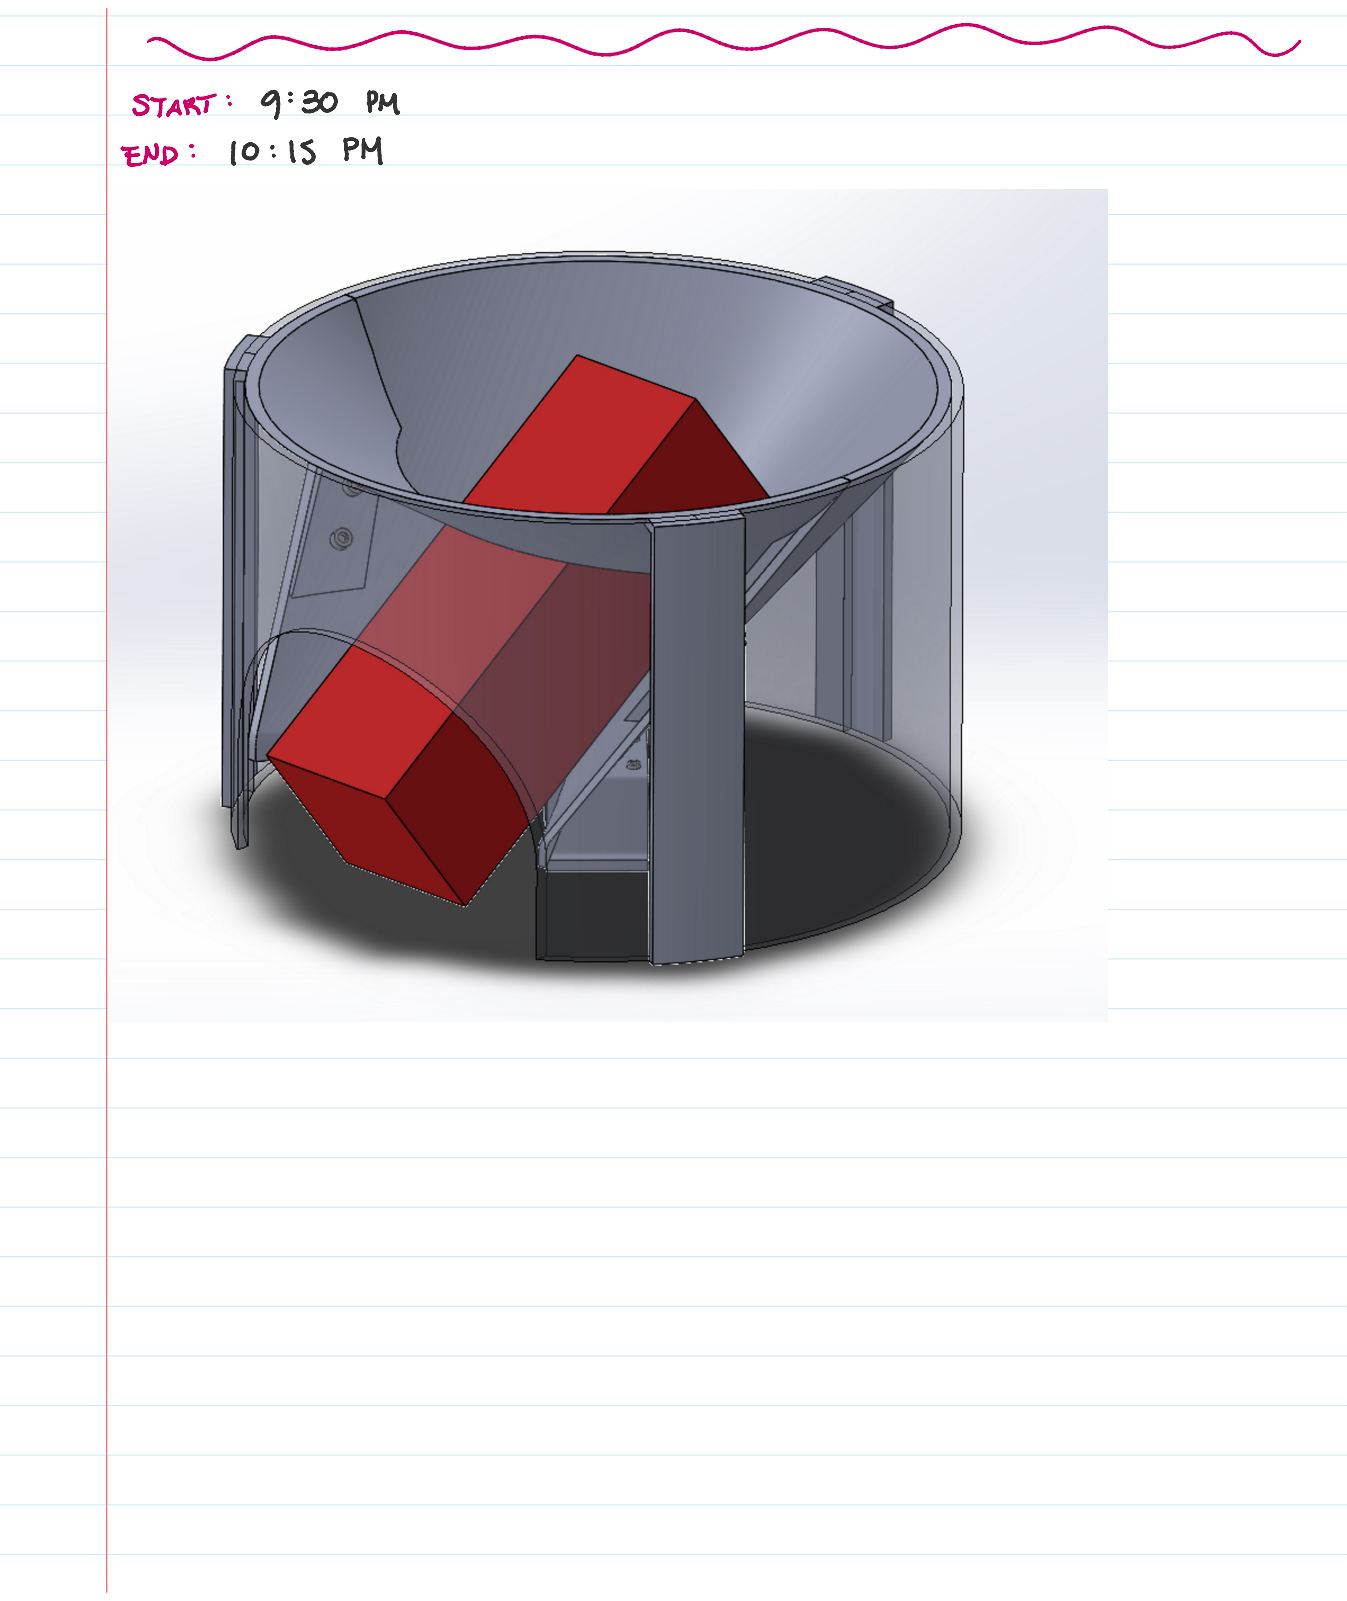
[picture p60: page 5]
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

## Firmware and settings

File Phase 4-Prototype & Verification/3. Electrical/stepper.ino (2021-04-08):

/*
 * Copied from 2448 motor driver information for driving stepper motors
 */
#include <Stepper.h>

// change this to the number of steps on your motor
#define STEPS 200

// create an instance of the stepper class, specifying
// the number of steps of the motor and the pins it's
// attached to
Stepper stepper(STEPS, 4, 5, 6, 7);  // CORRESPONDING PINS ON DRIVER MODULE: AIN2, AIN1, BIN1, BIN2

void setup() {
  Serial.begin(9600);
  pinMode(2, INPUT);
  Serial.println("Stepper test!");
  // set the speed of the motor to 30 RPMs
  stepper.setSpeed(60);
}

void loop() {
  Serial.println("Forward");
  stepper.step(STEPS);

  if (digitalRead(2) == HIGH) {
    while (digitalRead(2) == HIGH)
      delay(10);
    while (digitalRead(2) == LOW)
      delay (10);
  }

  Serial.println("Backward");
  stepper.step(-STEPS);
  
  if (digitalRead(2) == HIGH) {
    while (digitalRead(2) == HIGH)
      delay(10);
    while (digitalRead(2) == LOW)
      delay (10);
  }
}
